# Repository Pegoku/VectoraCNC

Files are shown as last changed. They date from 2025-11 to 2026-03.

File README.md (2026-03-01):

# VectoraCNC

VectoraCNC is a custom-designed desktop CNC machine that I built from scratch.  
It’s mainly made from 2020 and 2040 aluminum extrusions, linear rails, and NEMA 17 stepper motors.

The goal was simple: build a compact, rigid CNC that actually works well, without spending $1000+.

Total build cost: **~$400**

This project is focused on affordability, reliability, and being a solid base for future upgrades and mods.

## Why I Built This

I wanted a rigid desktop CNC to machine harder materials like aluminum, but most affordable machines use V-wheels instead of linear rails.
So I designed VectoraCNC to use **linear rails on all axes**, while still keeping the total cost around $400.

This is my attempt at building something serious, but still accessible for makers and students like me.

## Images

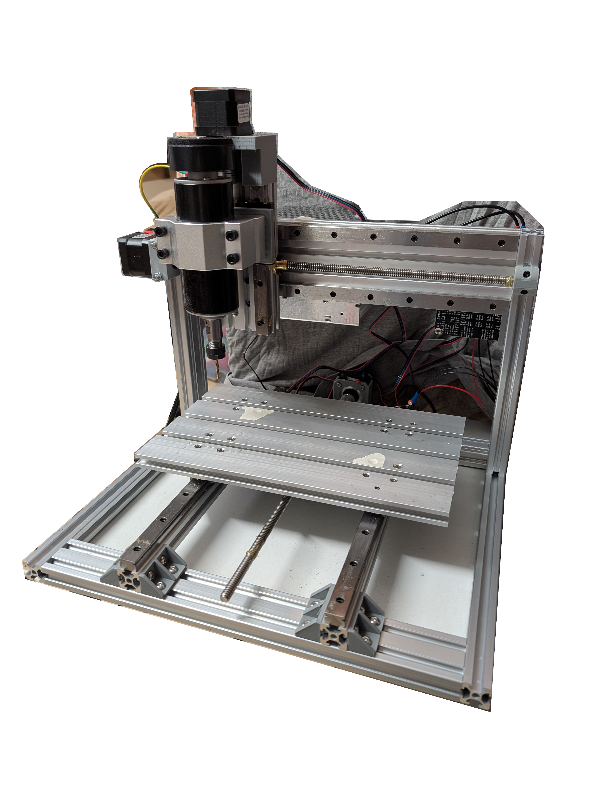
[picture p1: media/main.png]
main


<details>

<summary>CAD - click to expand</summary>

VectoraCNC CAD

</details>

## Features

- 230 × 160 × 80 mm Work Area  
- Rigid frame built with 2020 and 2040 aluminum extrusions  
- Linear rails on all axes for improved precision  
- NEMA 17 stepper motors with TMC2209 drivers  
- 15180 aluminum plate base  
- 500W spindle capable of cutting wood, plastics, and light aluminum  

## BOM (Bill of Materials)

Full parts list available here:
[ONLINE GOOGLE SHEETS](https://docs.google.com/spreadsheets/d/13GKgM2DIBkM6Ly_OZJB4GLy0vwwSqJ-mRrfgNgf3ems/edit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)

## Design Specifications

- **Build Volume**: 230 × 160 × 80 mm  
- **Bed Type**: 15180 300 mm T-Slot Aluminum Plate  
- **Spindle**: 500W ER11 Collet Spindle  
- **Stepper Motors**: NEMA 17 with TMC2209 Drivers  
- **Motion System**: Linear rail guided on all axes  
- **Control Board**: BIGTREETECH SKR V1.4  
- **Firmware**: Marlin (CNC mode)

## Wiring Diagram

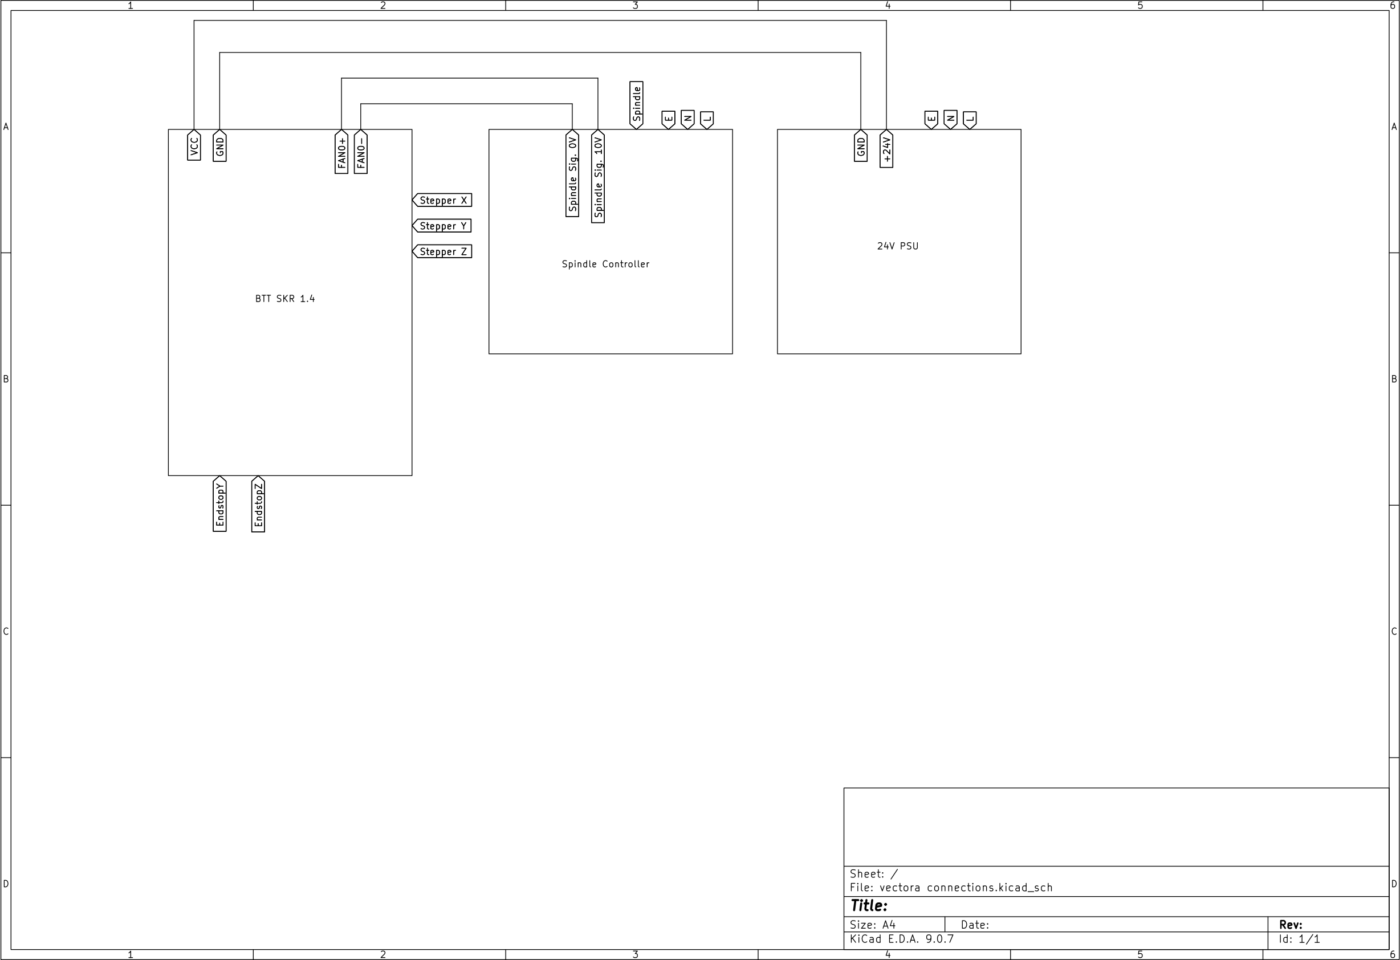
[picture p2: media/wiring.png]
Wiring Diagram


## Future Improvements

- Enclosure  
- Proper cable management  
- Stronger spindle  

This project is still evolving.

## License

This work is licensed under a
[Creative Commons Attribution-NonCommercial 4.0 International License][cc-by-nc].

[][cc-by-nc]

[cc-by-nc]: https://creativecommons.org/licenses/by-nc/4.0/
[cc-by-nc-image]: https://licensebuttons.net/l/by-nc/4.0/88x31.png
[cc-by-nc-shield]: https://img.shields.io/badge/License-CC%20BY--NC%204.0-lightgrey.svg

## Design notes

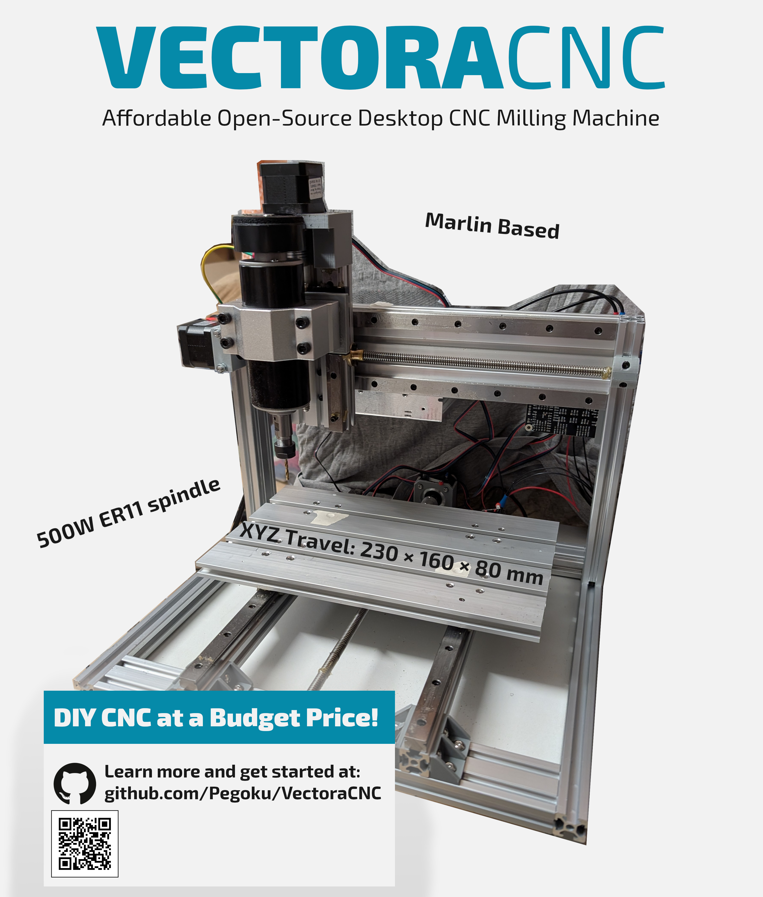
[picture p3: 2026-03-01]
media/VectoraCNC.jpg

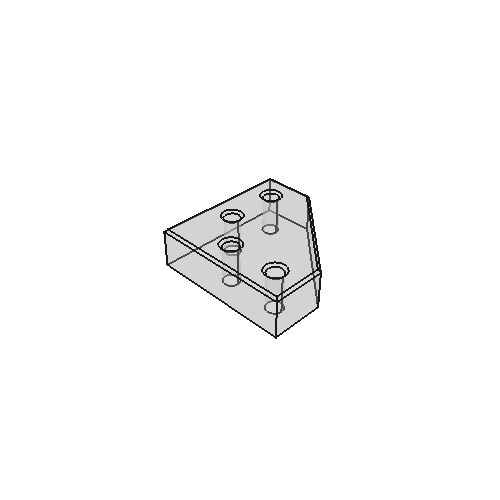
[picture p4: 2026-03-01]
CAD/baseimage_t.png

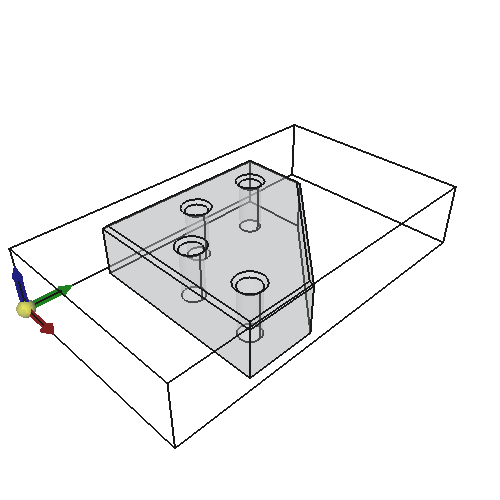
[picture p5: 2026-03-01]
CAD/datumImage_t.png

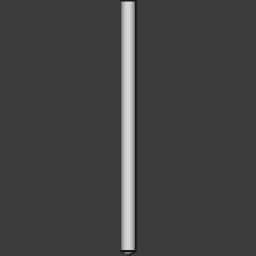
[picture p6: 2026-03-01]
CAD/T10.png

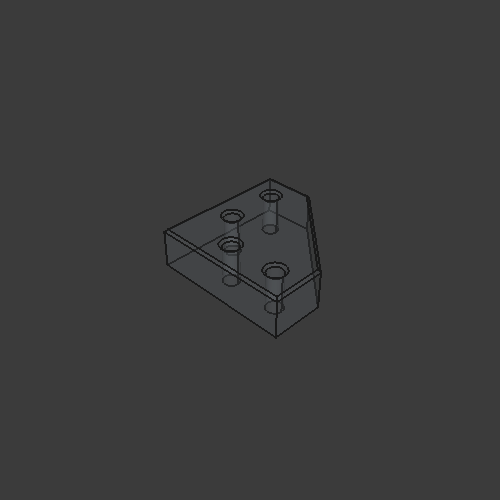
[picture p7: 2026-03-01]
CAD/baseimage.png

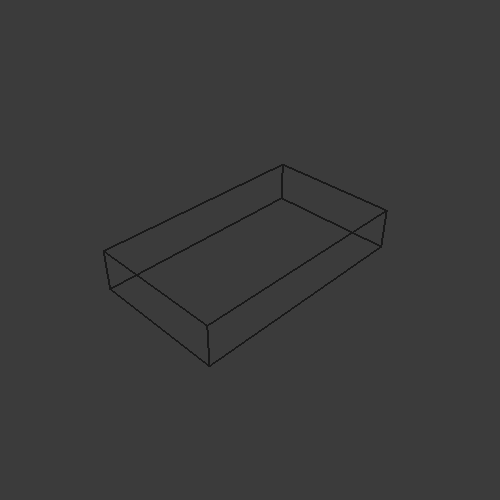
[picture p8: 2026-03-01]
CAD/stockImage.png

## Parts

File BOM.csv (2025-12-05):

Item | Qtty needed | Qtty / Pack | Pack Qtty | Price / pack | Source | Extra | Category | Already owned | Item Total | Final Total | Final Total ($)
Stepper Motor Nema 17 | 3 | 1 | 3 | 7.99€ | https://www.aliexpress.com/item/1005008459399126.html?mp=1 |  | Motor | FALSE | 23.97€ | 348.22€ | $405.72
USB B cable | 1 | 1 | 1 | 1.65€ | https://es.aliexpress.com/item/32700175631.html |  | Electronics | TRUE | 0
MainBoard | 1 | 1 | 1 | 37.39€ | https://es.aliexpress.com/item/1005006046426892.html | With TMC2209x5 | Electronics | FALSE | 37.39€
15180 extrusion | 1 | 1 | 1 | 20.99€ | https://www.aliexpress.com/item/1005007601829278.html?mp=1 | 300 mm | Bed | FALSE | 20.99€
Orange Pi zero | 0 | 1 | 0 | 21.11€ | https://es.aliexpress.com/item/1005005785695181.html |  | Electronics | FALSE | 0.00€
Spindle 500W | 1 | 1 | 1 | 83.90€ | https://es.aliexpress.com/item/1005008660257525.html?mp=1 |  | Spindle | FALSE | 83.90€
Endstops | 3 | 10 | 1 | 1.99€ | https://es.aliexpress.com/item/32273125391.html?mp=1 |  | Electronics | FALSE | 1.99€
2020 extrusion | 4 | 4 | 1 | 16.49€ | https://es.aliexpress.com/item/1005001598712011.html?mp=1 | 350 mm | Structure | FALSE | 16.49€
2040 extrusion | 2 | 1 | 2 | 7.49€ | https://es.aliexpress.com/item/1005002652962344.html?mp=1 | 350 mm | Structure | FALSE | 14.98€
2040 extrusion | 2 | 1 | 2 | 6.09€ | https://es.aliexpress.com/item/1005002652962344.html?mp=1 | 250 mm | Structure | FALSE | 12.18€
2080 extrusion | 1 | 1 | 1 | 14.19€ | https://es.aliexpress.com/item/1005002652962344.html?mp=1 | 350 mm | Structure | FALSE | 14.19€
2080 extrusion | 1 | 1 | 1 | 7.09€ | https://es.aliexpress.com/item/1005002652962344.html?mp=1 | 150 mm | Structure | FALSE | 7.09€
Lead Screw T8 | 1 | 1 | 1 | 2.66€ | https://www.aliexpress.com/item/1005009554037590.html?mp=1 | 150 mm | Linear | FALSE | 2.66€
Lead Screw T8 | 2 | 1 | 2 | 4.69€ | https://www.aliexpress.com/item/1005009554037590.html?mp=1 | 350 mm | Linear | FALSE | 9.38€
Linear Rail MGN15H | 4 | 1 | 4 | 14.79€ | https://es.aliexpress.com/item/1000007480470.html?mp=1 | 350 mm | Linear | FALSE | 59.16€
Linear Rail MGN15H | 2 | 1 | 2 | 8.89€ | https://es.aliexpress.com/item/1000007480470.html?mp=1 | 150 mm | Linear | FALSE | 17.78€
MGN15C block | 2 | 1 | 2 | 6.89€ | https://es.aliexpress.com/item/1000007480470.html?mp=1 |  | Linear | FALSE | 13.78€
5x8 coupling | 3 | 3 | 1 | 3.89€ | https://es.aliexpress.com/item/1005006305848755.html?mp=1 |  | Motor | FALSE | 3.89€
PWM to 0-10V | 1 | 1 | 1 | 3.19€ | https://es.aliexpress.com/item/1005006246628087.html?mp=1 |  | Electronics | FALSE | 3.19€
LRS-200-24 | 0 | 1 | 0 | 36.59€ | https://es.aliexpress.com/item/1005008946405294.html?mp=1 | Recommended, but unable to fit into budget | Electronics | FALSE | 0.00€
24V 250W PSU | 1 | 1 | 1 | 18.79€ | https://www.aliexpress.com/item/1005007294494572.html?mp=1 |  | Electronics | FALSE | 18.79€
M3 screw | 6 | 10 | 1 | 0.66€ | https://www.aliexpress.com/item/1005003189489793.html?mp=1 | 8 mm, ISO4762 | screws | TRUE | 0
M3 screw | 44 | 50 | 1 | 2.10€ | https://www.aliexpress.com/item/1005005832721555.html?mp=1 | 10 mm, ISO4762 | screws | FALSE | 2.10€
M3 screw | 7 | 10 | 1 | 0.68€ | https://www.aliexpress.com/item/1005003189489793.html?mp=1 | 12 mm, ISO4762 | screws | TRUE | 0
M3 screw | 8 | 50 | 1 | 2.09€ | https://www.aliexpress.com/item/1005004029818219.html?mp=1 | 14 mm, ISO10642 | screws | FALSE | 2.09€
M3 screw | 8 | 10 | 1 | 0.77€ | https://www.aliexpress.com/item/1005003189489793.html?mp=1 | 16 mm, ISO4762 | screws | FALSE | 0.77€
M3 screw | 16 | 50 | 1 | 2.51€ | https://www.aliexpress.com/item/1005004029818219.html?mp=1 | 18 mm, ISO10642 | screws | FALSE | 2.51€
M3 screw | 2 | 10 | 1 | 1.20€ | https://www.aliexpress.com/item/1005003189489793.html?mp=1 | 28 mm, ISO4762 | screws | FALSE | 1.20€
M3 screw | 4 | 10 | 1 | 1.72€ | https://www.aliexpress.com/item/1005003189489793.html?mp=1 | 38 mm, ISO4762 | screws | FALSE | 1.72€
M5 screw | 40 | 50 | 1 | 3.29€ | https://www.aliexpress.com/item/1005008380620769.html?mp=1 | 8 mm, ISO7380 | screws | FALSE | 3.29€
M5 screw | 2 | 10 | 1 | 1.32€ | https://www.aliexpress.com/item/1005003189489793.html?mp=1 | 12 mm, ISO4762 | screws | FALSE | 1.32€
M6 screw | 20 | 10 | 2 | 2.51€ | https://www.aliexpress.com/item/1005003189489793.html?mp=1 | 25 mm, ISO4762 | screws | FALSE | 5.02€
M3 T-Nut | 90 | 100 | 1 | 4.49€ | https://www.aliexpress.com/item/1005007383347166.html?mp=1 | 2020-M3-50PCS | screws | FALSE | 4.49€
M5 T-Nut | 42 | 50 | 1 | 3.09€ | https://www.aliexpress.com/item/1005007383347166.html?mp=1 | 2020-M5-50PCS | screws | FALSE | 3.09€
Corner Bracket | 4 | 20 | 1 | 3.99€ | https://www.aliexpress.com/item/1005007540068610.html?mp=1 | 2020 | Structure | TRUE | 0
Shipping | 1 | 1 | 1 | 0.71€ |  |  |  | FALSE | 0.71€
Discount code | 1 | 1 | 1 | -41.89€ |  | IFP03AUH |  | FALSE | -41.89€

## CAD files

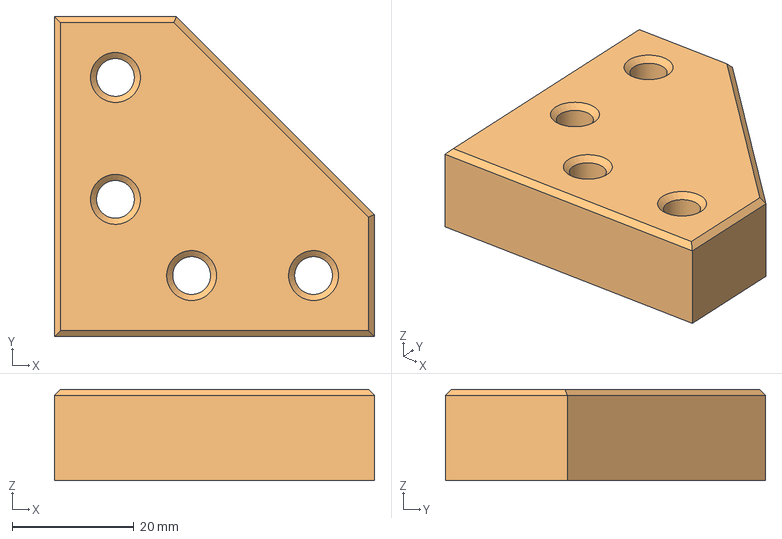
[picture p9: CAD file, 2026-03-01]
CAD/CNC test3.FCStd
52.5 x 52.5 x 15.0 mm
Model-Body
Stock-Body

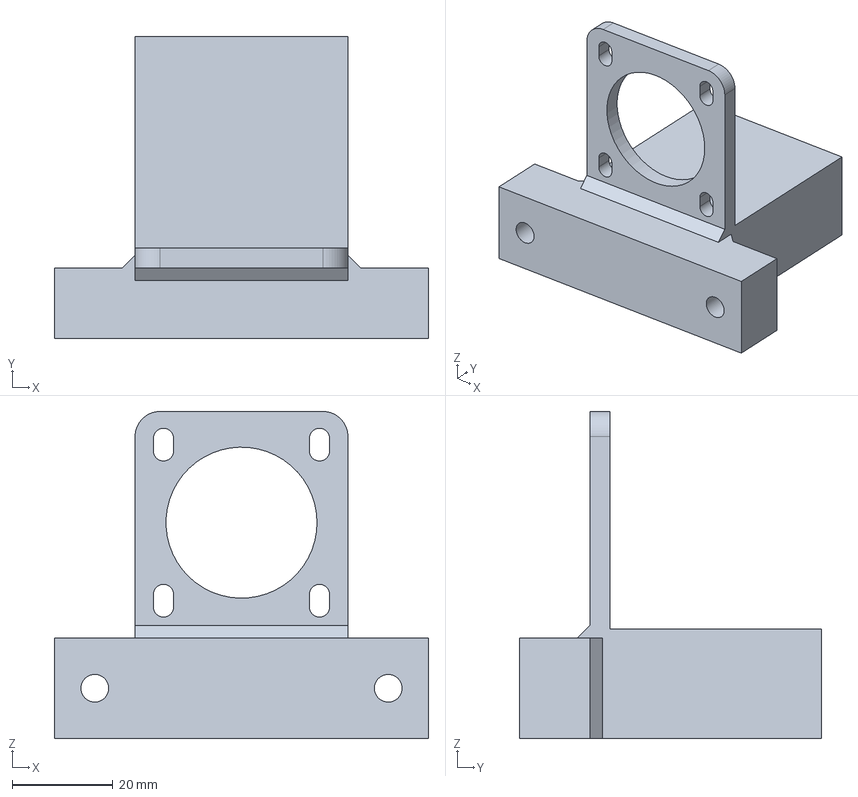
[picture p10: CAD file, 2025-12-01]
CAD/STEP/Printed/FrameYMotorSupport.step
74.3 x 60.0 x 65.0 mm

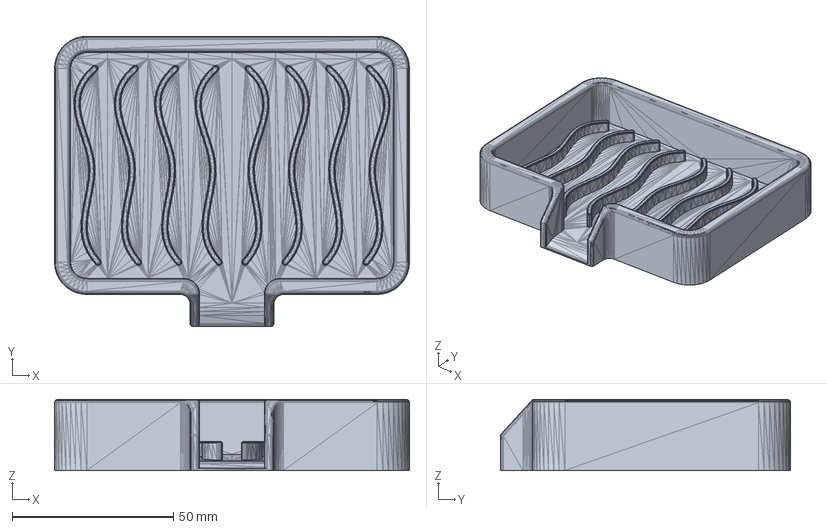
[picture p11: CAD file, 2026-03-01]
CAD/CNC test2.FCStd
110.0 x 90.0 x 22.0 mm

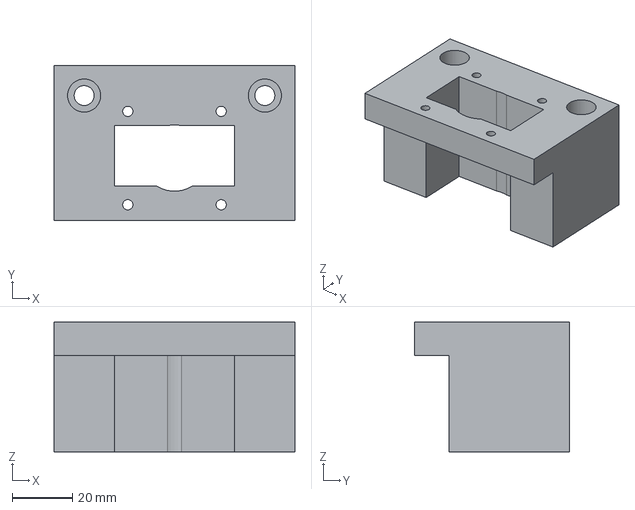
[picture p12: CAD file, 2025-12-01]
CAD/STEP/Printed/FrameZMotorSupport.step
80.0 x 51.5 x 43.0 mm

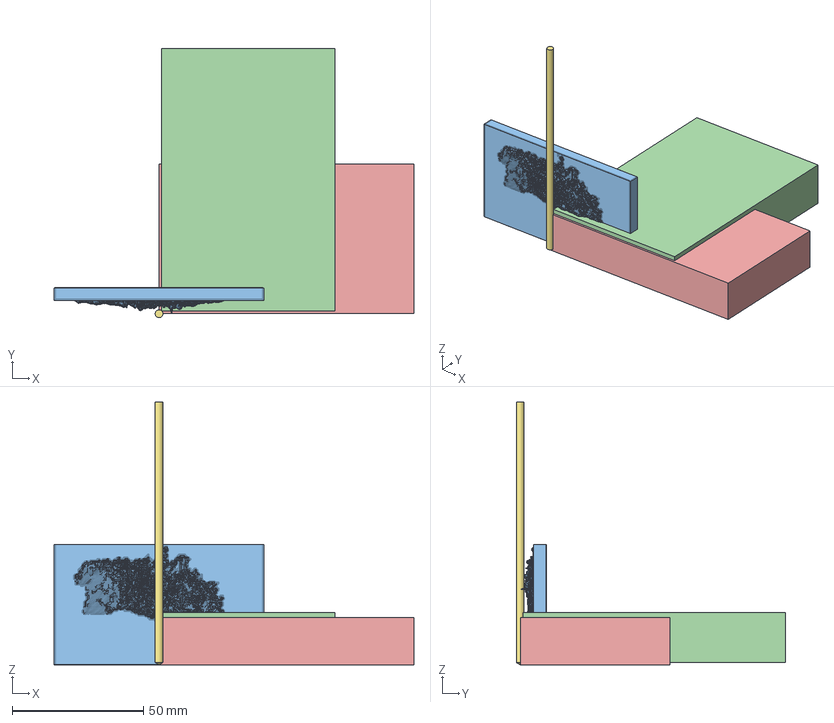
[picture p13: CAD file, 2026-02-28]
CAD/CNC test.FCStd
137.0 x 102.5 x 100.0 mm
Model-Servo to pot
Model-Lithophane_Screenshot_2026_02_28_at_13_53_57_Tangram_Heightmapper_png_1__stl_nanodlp_simplified_1_002 (Solid)
Lithophane_Screenshot_2026_02_28_at_13_53_57_Tangram_Heightmapper_png_1__stl_nanodlp_simplified_1_002
Stock001
Stock002
3mm_Drill
3mm_Drill001

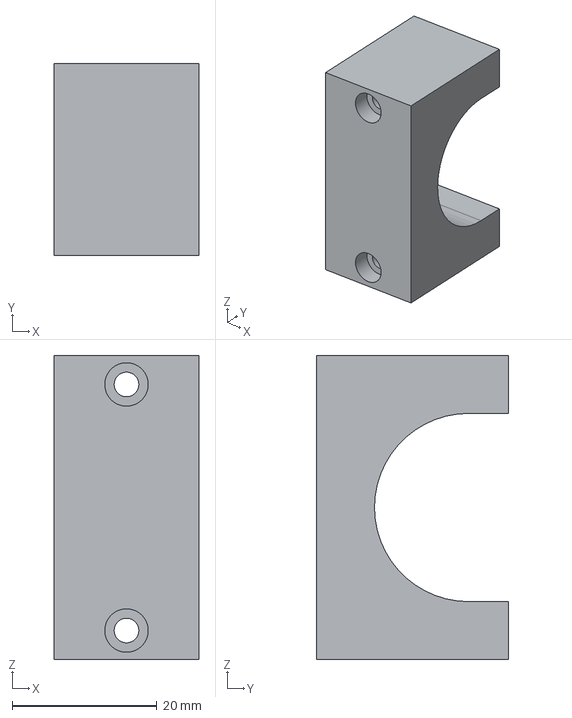
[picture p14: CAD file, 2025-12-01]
CAD/STEP/Printed/FrameXMotorSupport.step
20.0 x 26.5 x 42.0 mm

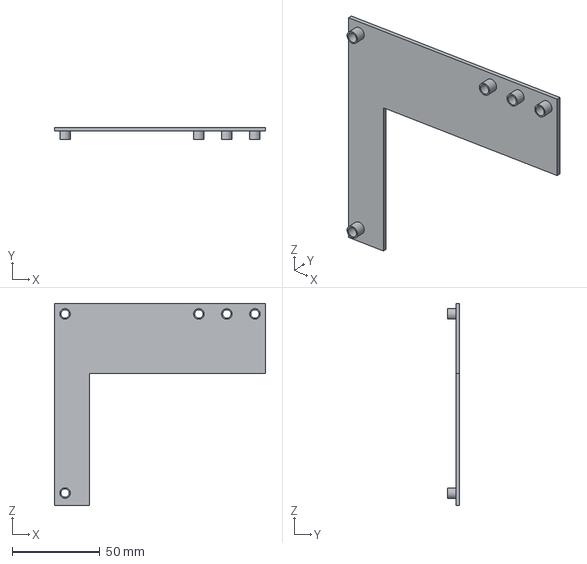
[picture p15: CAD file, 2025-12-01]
CAD/STEP/Printed/ElectronicsHolder.step
120.0 x 7.00 x 115.0 mm

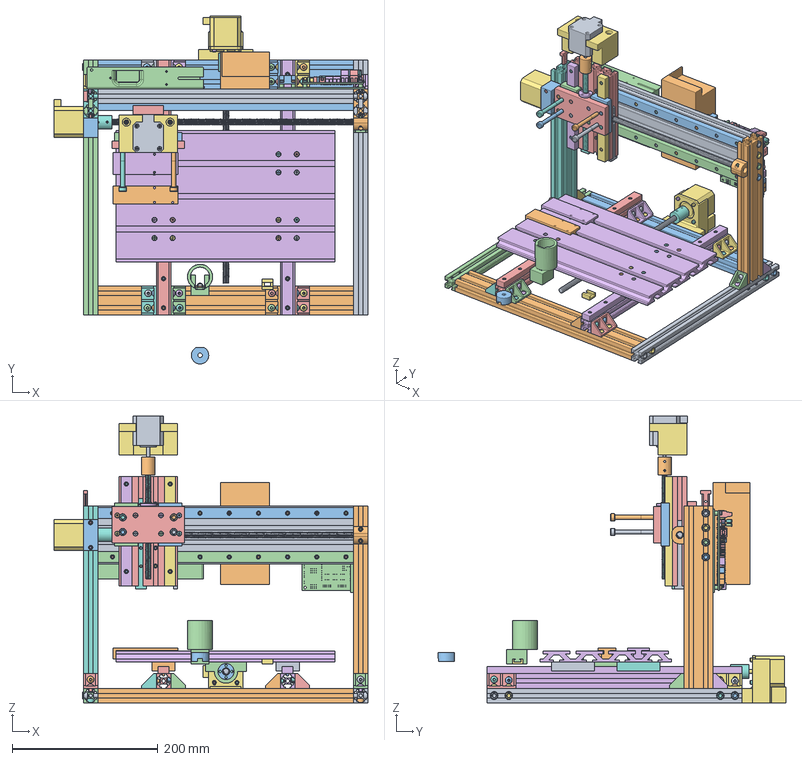
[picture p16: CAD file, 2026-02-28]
CAD/VectoraCNC.FCStd
430.0 x 476.9 x 393.0 mm
2020x30001
2020x30002
2020x30003
2020x30004
yMotorHolder
2040x250
2080x350
2040x25001
MGN15H rail003
MGN15H rail004
Linear RailSupport
MGN15H rail005
MGN15H rail006
T8 Lead Screw002
17HS4401003
Coupling 5x8002
MGN15H block007
MGN15H block008
AdapterPlate
T8 Nut002
ZmotorHolder
M3x16-Screw
M3x16-Screw016
M3x16-Screw017
M3x16-Screw018
M3x16-Screw019
M3x16-Screw020
M3x16-Screw021
M3x16-Screw022
M3x10-Screw176
M3x10-Screw184
M3x10-Screw185
M3x10-Screw186
M3x10-Screw187
M3x10-Screw188
M3x10-Screw189
M3x10-Screw190
M6x60-Screw012
M6x60-Screw014
M6x60-Screw013
M6x60-Screw
M3x14-Screw020
M3x14-Screw016
M3x14-Screw017
M3x14-Screw019
M3x14-Screw021
M3x14-Screw
M3x14-Screw022
M3x14-Screw018
MGN15C block002
MGN15C block001
M6 Spacer
17HS4401004
Coupling 5x8003
T8 Lead Screw003
LeadScrewHolder
MotorSupport
M3x10-Screw100
M3x10-Screw135
M3x10-Screw136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

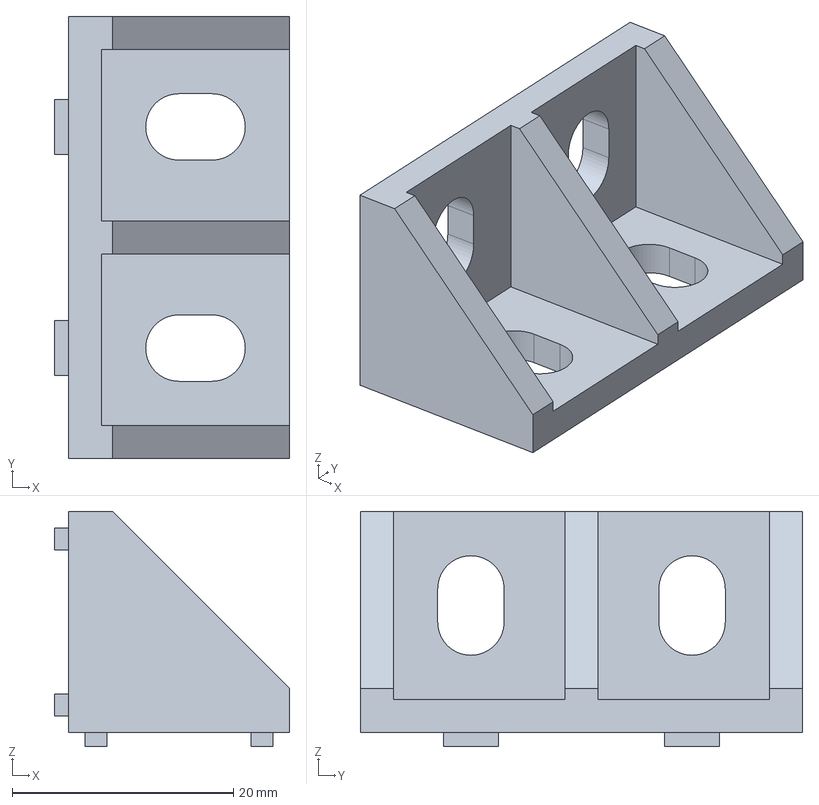
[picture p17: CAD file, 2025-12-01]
CAD/STEP/Printed/2040Corner.step
21.2 x 40.0 x 21.2 mm

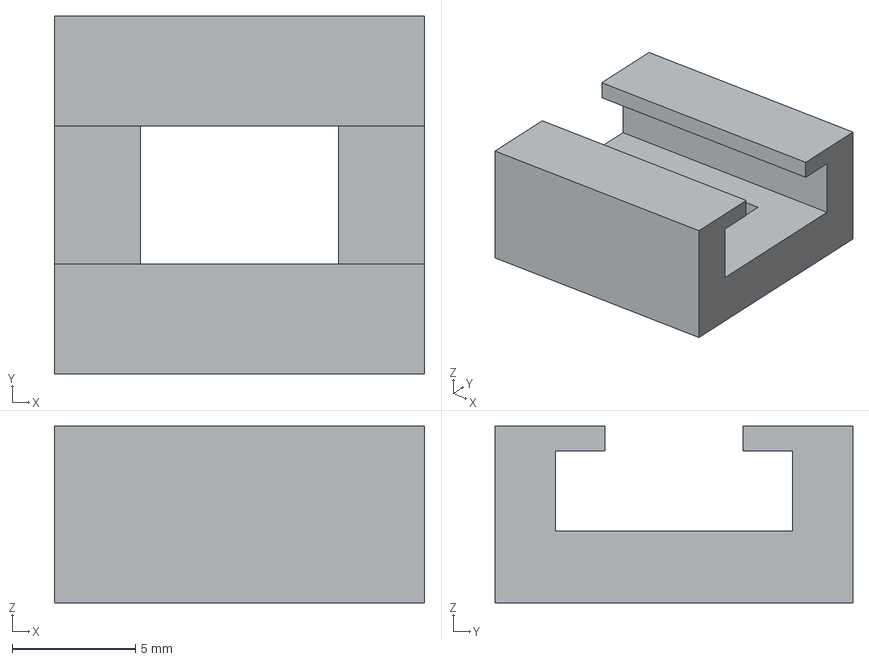
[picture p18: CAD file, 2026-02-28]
CAD/VectoraCNC-2020to1515.step
15.0 x 14.5 x 7.15 mm

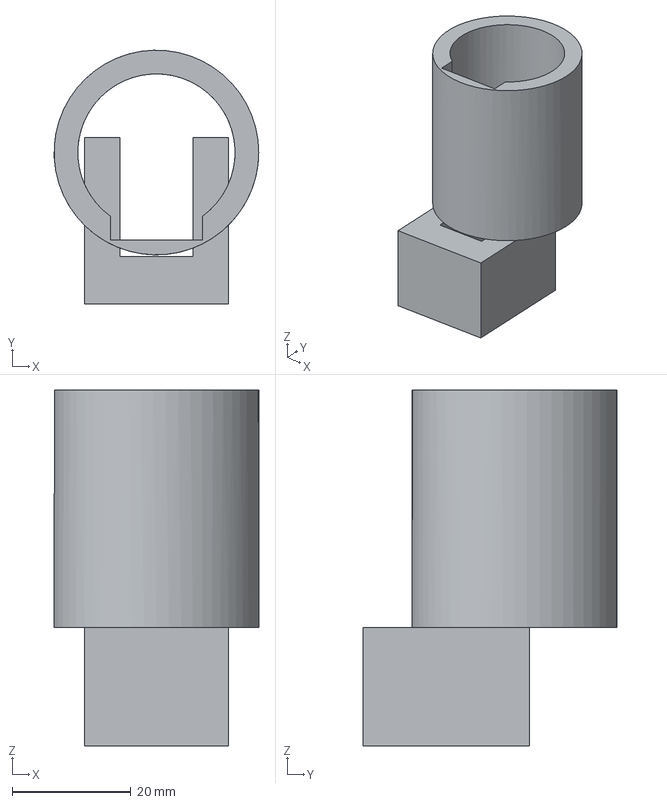
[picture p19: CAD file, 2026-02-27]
CAD/VectoraCNC-potHolder.step
34.5 x 42.7 x 60.0 mm

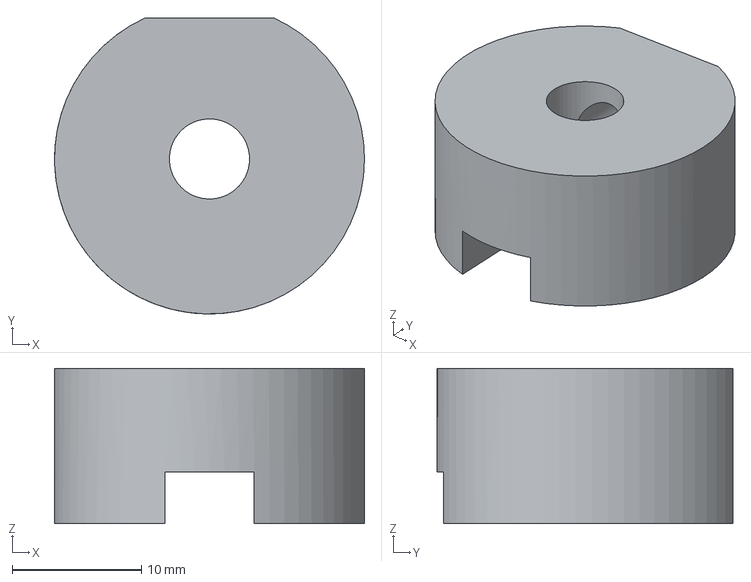
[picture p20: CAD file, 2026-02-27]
CAD/VectoraCNC-Servo to pot.step
24.0 x 22.9 x 12.0 mm

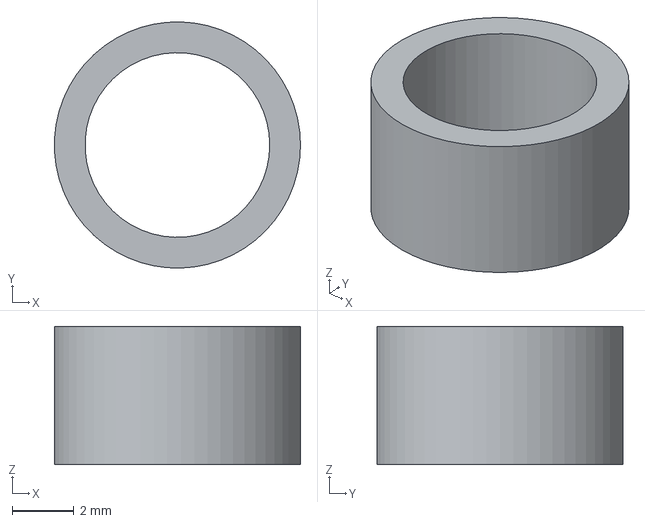
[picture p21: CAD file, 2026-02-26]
CAD/VectoraCNC-FrameM6 Spacer.step
7.99 x 8.00 x 4.50 mm

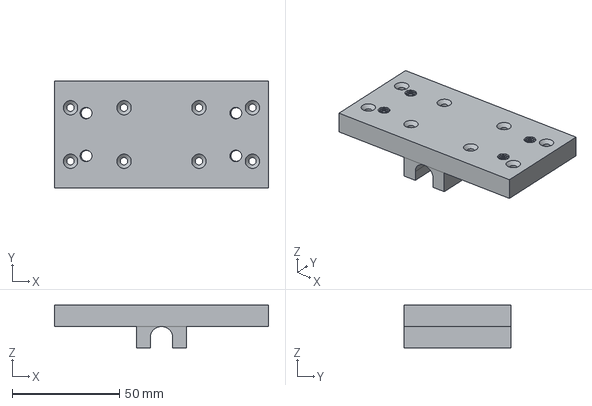
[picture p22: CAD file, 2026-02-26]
CAD/VectoraCNC-FrameAdapterPlate.step
100.0 x 50.0 x 20.0 mm

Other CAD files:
CAD/VectoraCNC-FrameZmotorHolder.step
CAD/VectoraCNC-FrameyMotorHolder.step
CAD/VectoraCNC-DrillMarker005.step
CAD/VectoraCNC-DrillMarker003.step
CAD/VectoraCNC-Body134.step
CAD/VectoraCNC-DrillMarker004.step
CAD/VectoraCNC-DrillMarker1.step
CAD/VectoraCNC-DrillMarker2.step
CAD/VectoraCNC-FrameLeadScrewHolder.step
CAD/VectoraCNC-FrameT8 Nut Holder.step
CAD/VectoraCNC-Storage2040 corner bracket.step

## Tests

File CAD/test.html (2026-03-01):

# Setup Report for CAM Job: Job

## Table of Contents

- Part Information
- Run Summary
- Rough Stock
- Tool Data
  - T10-3mm_Drill
- Output (G-code)
- Fixtures
- Squawks

## Part Information

Part

%{key} | %{val}

| Sequence | 1 of 1
| Job Type | 2.5D Milling
| CAD File | /home/pegoku/Media/Projects/Code/GitHub/VectoraCNC/CAD/CNC test3.FCStd
| Last Save | 2026-03-01T15:18:36Z
| Customer

## Run Summary

Operation | Minimum Z | Maximum Z | Coolant Mode | Cycle Time
MillFace | 0.00 mm | 23.00 mm | None | 00:22:09
Pocket3D | 0.00 mm | 23.00 mm | None | 00:58:47
Profile | 0.00 mm | 23.00 mm | None | 00:12:13

## Rough Stock

Material | Default
Surface Speed HSS
Surface Speed Carbide
X Size | 57.50 mm
Y Size | 98.00 mm
Z Size | 18.00 mm

## Tool Data

Description | 3mm_Drill
Manufacturer
Part Number
URL
Tool Shape | drill
Inspection Notes
Tool Diameter | 3.0 mm

Operation | Tool Controller | Feed Rate | Spindle Speed
MillFace | TC: 3mm_Drill | 10.0 mm/s | 12000.0

Operation | Tool Controller | Feed Rate | Spindle Speed
Pocket3D | TC: 3mm_Drill | 10.0 mm/s | 12000.0

Operation | Tool Controller | Feed Rate | Spindle Speed
Profile | TC: 3mm_Drill | 10.0 mm/s | 12000.0

## Output (G-code)

G-code File
Last Post Process Date
Stops | False
Programmer
Machine
Postprocessor | marlin
Post Processor Flags
File Size (kB) | 0.0
Line Count | 0

## Fixtures

Work Offsets | ['G54']
Order By | Fixture

Part Datum

## Squawks

Note | Operator | Date | Note
| CAMSanity | 2026-03-01 16:16:56.515838 | The Job has not been post-processed
| CAMSanity | 2026-03-01 16:16:56.515838 | Consider Specifying the Stock Material

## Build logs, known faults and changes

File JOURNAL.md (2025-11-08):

<!--
  ===================    !!READ THIS NOTICE!!   ====================
  DO NOT edit this file manually. Your changes WILL BE OVERWRITTEN!
  This journal is auto generated and updated by Hack Club Blueprint.
  To edit this file, please edit your journal entries on Blueprint.
  ==================================================================
-->

## 11/5/2025 - Start planning and design  

For this CNC, I'll want something big-ish that fits on a desk. Want it to be able to cut wood, plastics and some soft metals, e.g. aluminum, even if it's at a slow speed.

This is the idea:
The dimensions I have in mind are: 300x200x5.
Bed made out of some t-nut compatible shape, so I can clamp parts. I'll probably make it out of 2x 20100 x 300mm
Network connectivity, preferably wired. (probably using CNCjs)
Only **1** PSU.

This is the BOM I have for now. Prob will change many things
https://docs.google.com/spreadsheets/d/13GKgM2DIBkM6Ly_OZJB4GLy0vwwSqJ-mRrfgNgf3ems/edit?usp=sharing

Also, I started the CAD.
This is what I've got done for now.


## 11/7/2025 - Change plans  

Switching plans!
I found out about the 15180 aluminum extrusions (15x180) and they're cheaper, lighter and easier to use than 2x 20100 for the bed.
Also, I will probably go with linear rails, as they're stiffer than the linear shafts.

This is what I've got.



## 11/8/2025 12 PM - Switch to linear rails, and restructure the base  

I've modified the base so it now uses 2x mgn15H rails instead of the linear shafts.
I've also mostly finished the base structure.

The main problem with using Linear rails is I have no way to mount them to the bed, so I will have to drill the aluminum bed so I can screw it to the blocks. Hope it goes well.





## 11/8/2025 9 PM - Work on the X axis  

I've been working on the X axis.
I will use 2040 aluminum extrusions on the sides, and a 2080x350 to hold the main spindle. I will be using MGN15H for the X axis, and MGN12H for the Z axis.

This is what I've got so far: 


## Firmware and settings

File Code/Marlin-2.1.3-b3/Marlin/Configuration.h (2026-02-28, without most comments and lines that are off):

#pragma once
#define CONFIGURATION_H_VERSION 02010300
#define STRING_CONFIG_H_AUTHOR "(none, default config)" // Original author or contributor.
  #define MOTHERBOARD BOARD_BTT_SKR_V1_4
#define SERIAL_PORT -1
#define BAUDRATE 250000
#define X_DRIVER_TYPE  TMC2209
#define Y_DRIVER_TYPE  TMC2209
#define Z_DRIVER_TYPE  TMC2209
#define EXTRUDERS 0
#define DEFAULT_NOMINAL_FILAMENT_DIA 1.75
#define TEMP_SENSOR_0 0
#define TEMP_SENSOR_1 0
#define TEMP_SENSOR_2 0
#define TEMP_SENSOR_3 0
#define TEMP_SENSOR_4 0
#define TEMP_SENSOR_5 0
#define TEMP_SENSOR_6 0
#define TEMP_SENSOR_7 0
#define TEMP_SENSOR_BED 0
#define TEMP_SENSOR_PROBE 0
#define TEMP_SENSOR_CHAMBER 0
#define TEMP_SENSOR_COOLER 0
#define TEMP_SENSOR_BOARD 0
#define TEMP_SENSOR_SOC 0
#define TEMP_SENSOR_REDUNDANT 0
#define DUMMY_THERMISTOR_998_VALUE  25
#define DUMMY_THERMISTOR_999_VALUE 100
#if TEMP_SENSOR_IS_MAX_TC(0)
  #define MAX31865_SENSOR_OHMS_0      100 // (Ω) Typically 100 or 1000 (PT100 or PT1000)
  #define MAX31865_CALIBRATION_OHMS_0 430 // (Ω) Typically 430 for Adafruit PT100; 4300 for Adafruit PT1000
#endif
#if TEMP_SENSOR_IS_MAX_TC(1)
  #define MAX31865_SENSOR_OHMS_1      100
  #define MAX31865_CALIBRATION_OHMS_1 430
#endif
#if TEMP_SENSOR_IS_MAX_TC(2)
  #define MAX31865_SENSOR_OHMS_2      100
  #define MAX31865_CALIBRATION_OHMS_2 430
#endif
#if TEMP_SENSOR_IS_MAX_TC(BED)
  #define MAX31865_SENSOR_OHMS_BED      100
  #define MAX31865_CALIBRATION_OHMS_BED 430
#endif
#if HAS_E_TEMP_SENSOR
  #define TEMP_RESIDENCY_TIME         10  // (seconds) Time to wait for hotend to "settle" in M109
  #define TEMP_WINDOW                  1  // (°C) Temperature proximity for the "temperature reached" timer
  #define TEMP_HYSTERESIS              3  // (°C) Temperature proximity considered "close enough" to the target
#endif
#if TEMP_SENSOR_BED
  #define TEMP_BED_RESIDENCY_TIME     10  // (seconds) Time to wait for bed to "settle" in M190
  #define TEMP_BED_WINDOW              1  // (°C) Temperature proximity for the "temperature reached" timer
  #define TEMP_BED_HYSTERESIS          3  // (°C) Temperature proximity considered "close enough" to the target
#endif
#if TEMP_SENSOR_CHAMBER
  #define TEMP_CHAMBER_RESIDENCY_TIME 10  // (seconds) Time to wait for chamber to "settle" in M191
  #define TEMP_CHAMBER_WINDOW          1  // (°C) Temperature proximity for the "temperature reached" timer
  #define TEMP_CHAMBER_HYSTERESIS      3  // (°C) Temperature proximity considered "close enough" to the target
#endif
#if TEMP_SENSOR_REDUNDANT
  #define TEMP_SENSOR_REDUNDANT_SOURCE    E1  // The sensor that will provide the redundant reading.
  #define TEMP_SENSOR_REDUNDANT_TARGET    E0  // The sensor that we are providing a redundant reading for.
  #define TEMP_SENSOR_REDUNDANT_MAX_DIFF  10  // (°C) Temperature difference that will trigger a print abort.
#endif
#define HEATER_0_MINTEMP   5
#define HEATER_1_MINTEMP   5
#define HEATER_2_MINTEMP   5
#define HEATER_3_MINTEMP   5
#define HEATER_4_MINTEMP   5
#define HEATER_5_MINTEMP   5
#define HEATER_6_MINTEMP   5
#define HEATER_7_MINTEMP   5
#define BED_MINTEMP        5
#define CHAMBER_MINTEMP    5
#define HEATER_0_MAXTEMP 275
#define HEATER_1_MAXTEMP 275
#define HEATER_2_MAXTEMP 275
#define HEATER_3_MAXTEMP 275
#define HEATER_4_MAXTEMP 275
#define HEATER_5_MAXTEMP 275
#define HEATER_6_MAXTEMP 275
#define HEATER_7_MAXTEMP 275
#define BED_MAXTEMP      150
#define CHAMBER_MAXTEMP  60
#define HOTEND_OVERSHOOT 15   // (°C) Forbid temperatures over MAXTEMP - OVERSHOOT
#define BED_OVERSHOOT    10   // (°C) Forbid temperatures over MAXTEMP - OVERSHOOT
#define COOLER_OVERSHOOT  2   // (°C) Forbid temperatures closer than OVERSHOOT
#define PIDTEMP           // See the PID Tuning Guide at https://reprap.org/wiki/PID_Tuning
#define PID_MAX  255      // Limit hotend current while PID is active (see PID_FUNCTIONAL_RANGE below); 255=full current
#define PID_K1     0.95   // Smoothing factor within any PID loop
    #define DEFAULT_Kp  22.20
    #define DEFAULT_Ki   1.08
    #define DEFAULT_Kd 114.00
#define MAX_BED_POWER 255 // limits duty cycle to bed; 255=full current
#define MAX_CHAMBER_POWER 255 // limits duty cycle to chamber heater; 255=full current
  #define PID_FUNCTIONAL_RANGE 20 // If the temperature difference between the target temperature and the actual temperature
#define PREVENT_COLD_EXTRUSION
#define EXTRUDE_MINTEMP 170
#define PREVENT_LENGTHY_EXTRUDE
#define EXTRUDE_MAXLENGTH 200
#define THERMAL_PROTECTION_HOTENDS // Enable thermal protection for all extruders
#define THERMAL_PROTECTION_BED     // Enable thermal protection for the heated bed
#define THERMAL_PROTECTION_CHAMBER // Enable thermal protection for the heated chamber
#define THERMAL_PROTECTION_COOLER  // Enable thermal protection for the laser cooling
#define ENDSTOPPULLUPS
#define X_MIN_ENDSTOP_HIT_STATE HIGH
#define X_MAX_ENDSTOP_HIT_STATE HIGH
#define Y_MIN_ENDSTOP_HIT_STATE LOW
#define Y_MAX_ENDSTOP_HIT_STATE LOW
#define Z_MIN_ENDSTOP_HIT_STATE LOW
#define Z_MAX_ENDSTOP_HIT_STATE HIGH
#define I_MIN_ENDSTOP_HIT_STATE HIGH
#define I_MAX_ENDSTOP_HIT_STATE HIGH
#define J_MIN_ENDSTOP_HIT_STATE HIGH
#define J_MAX_ENDSTOP_HIT_STATE HIGH
#define K_MIN_ENDSTOP_HIT_STATE HIGH
#define K_MAX_ENDSTOP_HIT_STATE HIGH
#define U_MIN_ENDSTOP_HIT_STATE HIGH
#define U_MAX_ENDSTOP_HIT_STATE HIGH
#define V_MIN_ENDSTOP_HIT_STATE HIGH
#define V_MAX_ENDSTOP_HIT_STATE HIGH
#define W_MIN_ENDSTOP_HIT_STATE HIGH
#define W_MAX_ENDSTOP_HIT_STATE HIGH
#define Z_MIN_PROBE_ENDSTOP_HIT_STATE LOW
#define DEFAULT_AXIS_STEPS_PER_UNIT   { 1600, 1600, 1600 }
#define EDITABLE_STEPS_PER_UNIT
#define DEFAULT_MAX_FEEDRATE          { 12.5, 12.5, 2.5 }
#define DEFAULT_MAX_ACCELERATION      { 200, 200, 50 }
#define DEFAULT_ACCELERATION           200    // X, Y, Z and E acceleration for printing moves
#define DEFAULT_RETRACT_ACCELERATION   200    // E acceleration for retracts
#define DEFAULT_TRAVEL_ACCELERATION    200    // X, Y, Z acceleration for travel (non printing) moves
  #define JUNCTION_DEVIATION_MM 0.013 // (mm) Distance from real junction edge
  #define JD_HANDLE_SMALL_SEGMENTS    // Use curvature estimation instead of just the junction angle
#define Z_MIN_PROBE_USES_Z_MIN_ENDSTOP_PIN
#define NOZZLE_TO_PROBE_OFFSET { 10, 10, 0 }
#define PROBING_TOOL 0
#define PROBING_MARGIN 10
#define XY_PROBE_FEEDRATE    (133*60) // (mm/min)
#define Z_PROBE_FEEDRATE_FAST  (4*60) // (mm/min)
#define Z_PROBE_FEEDRATE_SLOW (Z_PROBE_FEEDRATE_FAST / 2) // (mm/min)
#define Z_CLEARANCE_DEPLOY_PROBE   10 // (mm) Z Clearance for Deploy/Stow
#define Z_CLEARANCE_BETWEEN_PROBES  5 // (mm) Z Clearance between probe points
#define Z_CLEARANCE_MULTI_PROBE     5 // (mm) Z Clearance between multiple probes
#define Z_PROBE_ERROR_TOLERANCE     3 // (mm) Tolerance for early trigger (<= -probe.offset.z + ZPET)
#define Z_PROBE_LOW_POINT          -2 // (mm) Farthest distance below the trigger-point to go before stopping
#define X_ENABLE_ON LOW
#define Y_ENABLE_ON LOW
#define Z_ENABLE_ON LOW
#define E_ENABLE_ON LOW // For all extruders
#define DISABLE_OTHER_EXTRUDERS   // Keep only the active extruder enabled
#define INVERT_X_DIR true
#define INVERT_Y_DIR true
#define INVERT_Z_DIR false
#define INVERT_E0_DIR false
#define INVERT_E1_DIR false
#define INVERT_E2_DIR false
#define INVERT_E3_DIR false
#define INVERT_E4_DIR false
#define INVERT_E5_DIR false
#define INVERT_E6_DIR false
#define INVERT_E7_DIR false
#define X_HOME_DIR -1
#define Y_HOME_DIR -1
#define Z_HOME_DIR -1
#define X_BED_SIZE 230
#define Y_BED_SIZE 180
#define X_MIN_POS 0
#define Y_MIN_POS 0
#define Z_MIN_POS 0
#define X_MAX_POS X_BED_SIZE
#define Y_MAX_POS Y_BED_SIZE
#define Z_MAX_POS 1000
#define MIN_SOFTWARE_ENDSTOPS
  #define MIN_SOFTWARE_ENDSTOP_X
  #define MIN_SOFTWARE_ENDSTOP_Y
  #define MIN_SOFTWARE_ENDSTOP_I
  #define MIN_SOFTWARE_ENDSTOP_J
  #define MIN_SOFTWARE_ENDSTOP_K
  #define MIN_SOFTWARE_ENDSTOP_U
  #define MIN_SOFTWARE_ENDSTOP_V
  #define MIN_SOFTWARE_ENDSTOP_W
#define MAX_SOFTWARE_ENDSTOPS
  #define MAX_SOFTWARE_ENDSTOP_X
  #define MAX_SOFTWARE_ENDSTOP_Y
  #define MAX_SOFTWARE_ENDSTOP_Z
  #define MAX_SOFTWARE_ENDSTOP_I
  #define MAX_SOFTWARE_ENDSTOP_J
  #define MAX_SOFTWARE_ENDSTOP_K
  #define MAX_SOFTWARE_ENDSTOP_U
  #define MAX_SOFTWARE_ENDSTOP_V
  #define MAX_SOFTWARE_ENDSTOP_W
#define Z_SAFE_HOMING
  #define Z_SAFE_HOMING_X_POINT 193       // (mm) X point for Z homing
  #define Z_SAFE_HOMING_Y_POINT 172       // (mm) Y point for Z homing
#define HOMING_FEEDRATE_MM_M { (8*60), (8*60), (4*60) }
#define VALIDATE_HOMING_ENDSTOPS
#define EEPROM_CHITCHAT       // Give feedback on EEPROM commands. Disable to save flash.
#define EEPROM_BOOT_SILENT    // Keep M503 quiet and only give errors during first load
#define HOST_KEEPALIVE_FEATURE        // Disable this if your host doesn't like keepalive messages
#define DEFAULT_KEEPALIVE_INTERVAL 2  // Number of seconds between "busy" messages. Set with M113.
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

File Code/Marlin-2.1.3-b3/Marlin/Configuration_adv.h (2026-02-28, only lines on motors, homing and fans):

#define E0_AUTO_FAN_PIN -1
#define E1_AUTO_FAN_PIN -1
#define E2_AUTO_FAN_PIN -1
#define E3_AUTO_FAN_PIN -1
#define E4_AUTO_FAN_PIN -1
#define E5_AUTO_FAN_PIN -1
#define E6_AUTO_FAN_PIN -1
#define E7_AUTO_FAN_PIN -1
#define CHAMBER_AUTO_FAN_PIN -1
#define COOLER_AUTO_FAN_PIN -1
#define HOMING_BUMP_MM      { 0, 0, 2 }       // (linear=mm, rotational=°) Backoff from endstops after first bump
#define HOMING_BUMP_DIVISOR { 2, 2, 4 }       // Re-Bump Speed Divisor (Divides the Homing Feedrate)
#define MICROSTEP_MODES { 16, 16, 16, 16, 16, 16 } // [1,2,4,8,16]
    #define X_CURRENT       1000       // (mA) RMS current. Multiply by 1.414 for peak current.
    #define X_CURRENT_HOME   600       // (mA) RMS current for homing. Lower helps sensorless homing reliability.
    #define X_MICROSTEPS     16        // 0..256
    #define Y_CURRENT       1000
    #define Y_CURRENT_HOME   600
    #define Y_MICROSTEPS     16
    #define Z_CURRENT       1000
    #define Z_CURRENT_HOME   700
    #define Z_MICROSTEPS     16
  #define X_HYBRID_THRESHOLD     100  // [mm/s]
  #define X2_HYBRID_THRESHOLD    100
  #define Y_HYBRID_THRESHOLD     100
  #define Y2_HYBRID_THRESHOLD    100
  #define Z_HYBRID_THRESHOLD       3
  #define Z2_HYBRID_THRESHOLD      3
  #define Z3_HYBRID_THRESHOLD      3
  #define Z4_HYBRID_THRESHOLD      3
  #define I_HYBRID_THRESHOLD       3  // [linear=mm/s, rotational=°/s]
  #define J_HYBRID_THRESHOLD       3  // [linear=mm/s, rotational=°/s]
  #define K_HYBRID_THRESHOLD       3  // [linear=mm/s, rotational=°/s]
  #define U_HYBRID_THRESHOLD       3  // [mm/s]
  #define V_HYBRID_THRESHOLD       3
  #define W_HYBRID_THRESHOLD       3
  #define E0_HYBRID_THRESHOLD     30
  #define E1_HYBRID_THRESHOLD     30
  #define E2_HYBRID_THRESHOLD     30
  #define E3_HYBRID_THRESHOLD     30
  #define E4_HYBRID_THRESHOLD     30
  #define E5_HYBRID_THRESHOLD     30
  #define E6_HYBRID_THRESHOLD     30
  #define E7_HYBRID_THRESHOLD     30
  #define SENSORLESS_HOMING // StallGuard capable drivers only
    #define X_STALL_SENSITIVITY  60
    #define X2_STALL_SENSITIVITY X_STALL_SENSITIVITY
    #define IMPROVE_HOMING_RELIABILITY
#define CNC_HOMING_ROUTINE

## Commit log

2025-11-05 start design
    [VectoraCNC.FCStd]
2025-11-05 continue with cad
    [VectoraCNC.FCStd]
2025-11-06 add bottom frame strucute and motor
    [VectoraCNC.FCStd]
2025-11-08 switch to Linear rails for the base, and finish the base movement part
    [VectoraCNC.FCStd]
2025-11-08 work on X axis
    [VectoraCNC.FCStd]
2025-11-09 continue with x axis
    [VectoraCNC.FCStd]
2025-11-09 add spindle assembly
    [VectoraCNC.FCStd]
2025-11-14 Work on MotorMount
    [VectoraCNC.FCStd, VectoraCNC.sync-conflict-20251110-141944-YXYCSNO.FCStd]
2025-11-14 remove sync conflict
    [VectoraCNC.sync-conflict-20251110-141944-YXYCSNO.FCStd]
2025-11-15 continue holder
    [VectoraCNC.FCStd]
2025-11-16 finish Spindle support
    [VectoraCNC.FCStd]
2025-11-22 work on cnc
    [VectoraCNC.FCStd]
2025-11-23 finish Z axis
    [VectoraCNC.FCStd]
2025-11-23 continue X axis
2025-11-24 finish X axis
2025-11-29 X motor support
2025-11-29 add 90º printed corner bracket
2025-11-30 finish corner bracket
2025-11-30 corners to Y axis
2025-11-30 holes to extrusions
2025-11-30 moar screws
2025-11-30 screws +
2025-11-30 screw screw screw
2025-11-30 Screw it
2025-12-01 add STEPs
    [2040Corner.step, ElectronicsHolder.step, FrameXMotorSupport.step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]
2025-12-01 add marlin
2025-12-01 add marlin repo
    [Configuration.h, Configuration_adv.h, esp32.csv]
2025-12-01 basic marlin config
    [Configuration.h, Configuration_adv.h]
2025-12-02 remove extruder from config
    [Configuration.h, Configuration_adv.h]
2025-12-27 Enable realtime reporting for better compatibility with software like CNCJS
    [Configuration_adv.h]
2025-12-27 Z Homing Sequence
2025-12-27 Enable Z homing macro
    [Configuration_adv.h]
2025-12-27 Refine CNC homing routine and tool length probing sequence
    [Configuration_adv.h]
2026-02-23 hole template 1
    [VectoraCNC-Body134.step, VectoraCNC.FCStd]
2026-02-23 drillMarkers + 2020 Tnut to 15180
    [VectoraCNC-2020to1515.step, VectoraCNC-Body134.step, VectoraCNC-DrillMarker1.step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]
2026-02-23 fix 2040 corner brackets
    [VectoraCNC-Storage2040 corner bracket.step, VectoraCNC.FCStd]
2026-02-24 more drillMarkers
    [VectoraCNC-DrillMarker003.step, VectoraCNC-DrillMarker004.step, VectoraCNC-FrameAdapterPlate.step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]
2026-02-26 motor holder fix
    [VectoraCNC-FrameyMotorHolder.step, VectoraCNC.FCStd]
2026-02-26 ADAPTER PLATE FIX
    [VectoraCNC.FCStd]
2026-02-26 z motor mount fix
    [VectoraCNC-FrameZmotorHolder.step, VectoraCNC.FCStd]
2026-02-26 M6 spacer
    [VectoraCNC-FrameM6 Spacer.step, VectoraCNC.FCStd]
2026-02-27 Fix serial port
    [Configuration.h]
2026-02-27 apply cap to pwm
    [Configuration_adv.h]
2026-02-27 servo adapter
    [VectoraCNC-Servo to pot.step, VectoraCNC.FCStd]
2026-02-27 potentiometer holder
    [VectoraCNC-potHolder.step]
2026-02-27 sensorless homing
    [Configuration_adv.h]
2026-02-27 test cnc cam and configs
    [CNC test.FCStd, Configuration.h, Configuration_adv.h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]
2026-02-27 max speeds
    [Configuration.h, Configuration_adv.h]
2026-02-27 homing works
    [Configuration.h, Configuration_adv.h]
2026-02-27 use RPM instead of PWM
    [Configuration_adv.h]
2026-02-28 CAM Test1
    [CNC test.FCStd]
2026-02-28 CNC CAM
    [CNC test.FCStd]
2026-02-28 Fix Tnut adapters
    [VectoraCNC-2020to1515.step, VectoraCNC.FCStd]
2026-02-28 CAM Test
    [CNC test.FCStd]
2026-02-28 remove "soft endstop"
    [Configuration.h, Configuration_adv.h]
2026-02-28 CAM tests
    [CNC test2.FCStd, CNC test3.FCStd]
2026-03-01 improve CAM
    [CNC test3.FCStd]
2026-03-01 Deburr / Chamfer
    [CNC test3.FCStd]
2026-03-01 Deburr / Chamfer order fix
    [CNC test3.FCStd]
2026-03-01 6mm spindle speed fix
    [CNC test3.FCStd]

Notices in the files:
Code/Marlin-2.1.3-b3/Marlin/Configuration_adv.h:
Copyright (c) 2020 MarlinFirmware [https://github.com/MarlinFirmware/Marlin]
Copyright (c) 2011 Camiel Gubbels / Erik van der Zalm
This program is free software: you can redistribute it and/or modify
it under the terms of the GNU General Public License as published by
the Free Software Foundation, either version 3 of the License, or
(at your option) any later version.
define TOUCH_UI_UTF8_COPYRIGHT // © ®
